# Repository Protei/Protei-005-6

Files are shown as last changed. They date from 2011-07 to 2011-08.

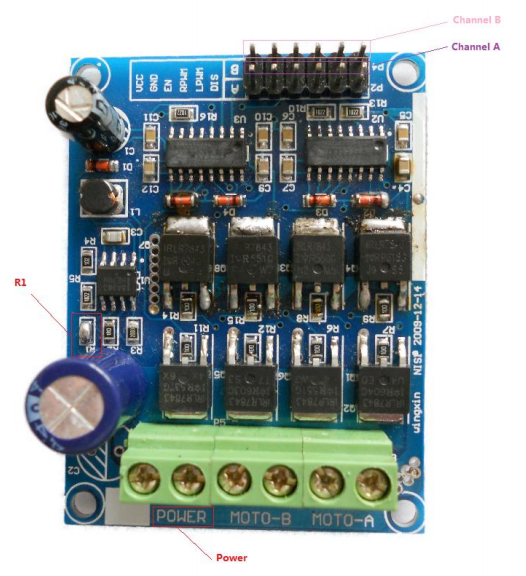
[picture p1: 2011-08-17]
Documentation/images/motordriver.png

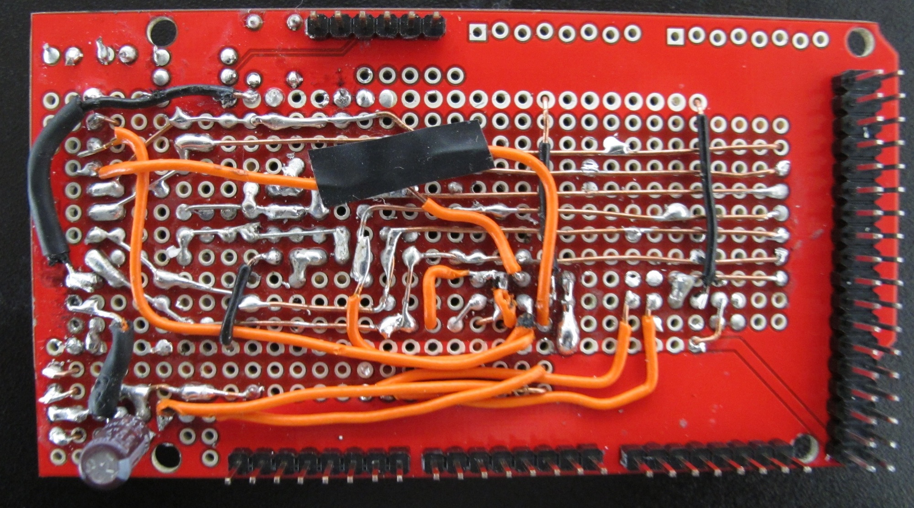
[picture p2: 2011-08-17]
Documentation/images/IMG_1639.JPG

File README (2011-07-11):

This is the git repository for the Protei project (http://protei.org).

This is  a place  for storing and  building upon code,  storing  electrical
schematics and mechanical drawings,  and for storing basically any piece of
digital information  developed for the Protei project. Storing  things here
allows us to keep a record of changes and contributions.

To gain write access to this repository, please email code@opensailing.net.

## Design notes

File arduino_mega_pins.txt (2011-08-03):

MOTOR DRIVER 1
ENA - 42
ENB - 44
RPWMA - 4
RPWMB - 5
LPWMA - 6
LPWMB - 7

MOTOR DRIVER 2
ENA - 36
RPWMA - 8
LPWMA - 9

XBEE
pin 18/19 (Serial 1)

MOTOR SENSORS
ROT1 - 2 (interrupt 0)
ROT2 - 3 (interrupt 1)
L2B - 48
L2A - 46
L1B - 40
L1A - 38
ROTWINCH - 21 (interrupt 2)
LIMITWINCH - 50git

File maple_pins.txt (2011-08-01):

MAPLE PIN		CONNECTION	REQUIRED FUNCTIONALITY	MAPLE HARDWARE DEVICE
MOTOR DRIVER 1			
4			ENA					DI/O
0			RPWMA		PWM			Timer 2
1			LPWMA		PWM			Timer 2
5			ENB					DI/O
2			RPWMB		PWM			Timer 2
3			LPWMB		PWM			Timer 2
XBEE			
7			XBDIN		Tx			USART 1
8			XBDOUT		Rx			USART 1
MOTOR DRIVER 2			
6			ENA					DI/O
11			RPWMA		PWM			Timer 3
12			LPWMA		PWM			Timer 3
MOTOR FEEDBACK			
29			ROT1		int			EXTI10
21			LIMIT1A		int			EXTI13
28			LIMIT1B		int			EXTI9
30			ROT2		int			EXTI11
22			LIMIT2A		int			EXTI14
37			LIMIT2B		int			EXTI8
31			ROTW		int			EXTI12
23			LIMITWA		int			EXTI15

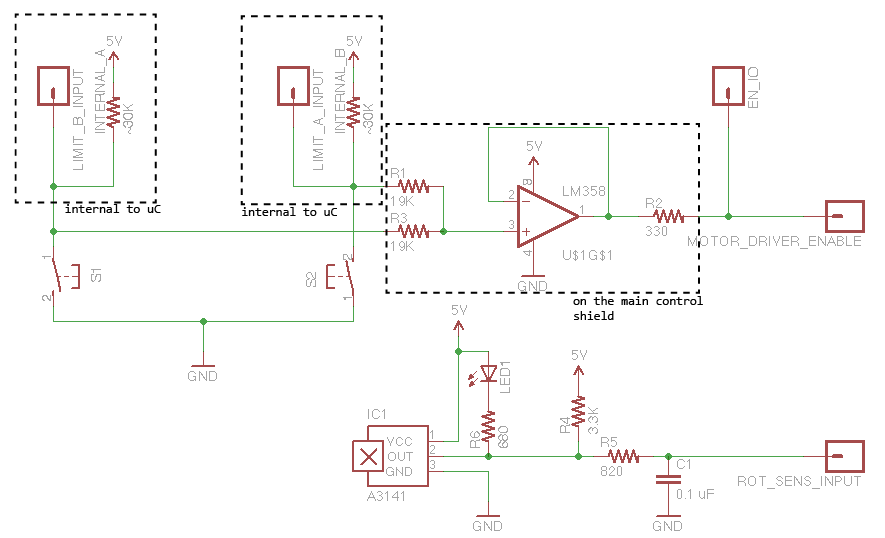
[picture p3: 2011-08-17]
Actuator/actuator.png

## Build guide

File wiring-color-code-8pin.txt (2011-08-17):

WIRING COLOR CODE : KEEL <-> CONTROL BOX

COLOR		NAME		EXPLANATION

Gray		L1A			Limit Switch A 	for motor 1
White		L1B			Limit Switch B 	for motor 1
Brown		L2A			Limit Switch A 	for motor 2
Green		L2B			Limit Switch B 	for motor 2
Yellow		ROT1		Rotation Sensor for motor 1
Blue		ROT2		Rotation Sensor for motor 2
Black		GND			Ground
Red			VCC			Power Supply +5V

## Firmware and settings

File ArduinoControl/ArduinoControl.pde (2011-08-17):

/*
	Protei — Remote Control and Motor Control
 Copyright (C) 2011  Logan Williams, Gabriella Levine,
                     Qiuyang Zhou, Francois de la Taste
 
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
 You should have received a copy of the GNU General Public License
 along with this program (see COPYING).  If not, see <http://www.gnu.org/licenses/>.
 */
 
#include "consts.h" 	        // File containing constants defininitions
#include "comm.h"	 	// File containing communication subroutines
//#include "motor.h"		// File containing motor control subroutines
#include "motor_controller.h"

// EXECUTION VARIABLES
unsigned long lastExecuted; // this variable keeps
unsigned long time; // this is a variable for the current time

// for 19 jul test

int motorNumber;
int stopwatch;

unsigned long lastBowCounted;
unsigned long lastSternCounted;

unsigned long usbElapsCounter = 0;

Motor bow;
MotorController bowController;

Motor stern;
MotorController sternController;

Motor winch;

void setup() {
  bow.init(BOW);
  bowController.init(&bow, GAIN[BOW]);
  pinMode(ROT_PINS[BOW], INPUT);
  attachInterrupt(ROT_INTS[BOW], countBow, FALLING); //was set to CHANGE... it shouldn't make a difference (but you never know)

  stern.init(STERN);
  sternController.init(&stern, GAIN[STERN]);
  pinMode(ROT_PINS[STERN], INPUT);
  attachInterrupt(ROT_INTS[STERN], countStern, FALLING);
  
  winch.init(WINCH);
  pinMode(ROT_PINS[WINCH], INPUT);

  // initialize pins
  pinMode(EN_PINS[BOW], INPUT);
  pinMode(EN_PINS[STERN], INPUT);
  pinMode(EN_PINS[WINCH], INPUT);

  pinMode(LIMIT_A_PINS[BOW], INPUT);
  pinMode(LIMIT_A_PINS[STERN], INPUT);
  pinMode(LIMIT_A_PINS[WINCH], INPUT);
  pinMode(LIMIT_B_PINS[BOW], INPUT);
  pinMode(LIMIT_B_PINS[STERN], INPUT);
  digitalWrite(LIMIT_A_PINS[BOW], HIGH);
  digitalWrite(LIMIT_A_PINS[STERN], HIGH);
  digitalWrite(LIMIT_A_PINS[WINCH], HIGH);
  digitalWrite(LIMIT_B_PINS[BOW], HIGH);
  digitalWrite(LIMIT_B_PINS[STERN], HIGH); 
  
  pinMode(LPWM_PINS[BOW], OUTPUT);
  pinMode(LPWM_PINS[STERN], OUTPUT);
  pinMode(LPWM_PINS[WINCH], OUTPUT);
  pinMode(RPWM_PINS[BOW], OUTPUT);
  pinMode(RPWM_PINS[STERN], OUTPUT);
  pinMode(RPWM_PINS[WINCH], OUTPUT);

  // start the interrupts
  interrupts(); 

  Serial1.begin(57600); // begin Xbee serial comms
  Serial.begin(115200); // begin USB serial comms
}

/*** THE MAIN LOOP ***
 * The loop body executes every 50ms, for a 20Hz control loop. This is kept in time with millis().
 */
void loop() {
  unsigned char data1 = 0x00;
  unsigned char data2 = 0x00;
  unsigned char data3 = 0x00;

  time = millis();
  
  // The main control loop executes every 50 ms (CONTROL_LOOP_PERIOD)
  if (((time - lastExecuted) > CONTROL_LOOP_PERIOD) || ((time - lastExecuted) < 0)) {
    lastExecuted = time; // update our time watch
    
    // If we have received new data from the Xbee, use it to update desired position
    if (receive(&data1, &data2, &data3)) { //fixmelater
      sendStatus(bow.getCntFlag(), stern.getCntFlag());
      //bowController.setTarget(map(data1, 0, 255, 0, MAX_MOTOR_ROTATIONS[BOW]));
      // testing two different control strategies:
      //  - closed loop position control (stern)
      //  - open loop speed control (bow)
      bow.move(map(data1, 0, 255, -255, 255));
      //stern.move(map(data2, 0, 255, -255, 255));
      //sternController.setTarget(map(data2, 0, 255, 0, MAX_MOTOR_ROTATIONS[STERN]));
      winch.move(map(data3, 0, 255, -255, 255));
    }

    //int output = bowController.runLoop();
    //int output2 = sternController.runLoop();

    if(debug && (usbElapsCounter >=  usbDebugRate) ) {
      Serial.println("BOW DEBUG DATA");
      bowController.printDebug();
      Serial.println("STERN DEBUG DATA");
      sternController.printDebug();
    }
    
    usbElapsCounter++;
  }
}

/** INTERRUPT SERVICE ROUTINES */
//    These really should be part of the Motor class
//    but the Arduino environment does not allow
//    interrupts to be defined inside objects
void countBow() {
  if (millis() - lastBowCounted > 40 || millis() - lastBowCounted < 0) { // this essentially "debounces" our rotation sensor
    if (digitalRead(ROT_PINS[BOW]) == LOW) { // double check
      lastBowCounted = millis(); // reset the timer
      bow.count(); // modify the counter accordingly
    }
  }
}

/* this is the same as above */
void countStern() {
  if (millis() - lastSternCounted > 40 || millis() - lastSternCounted < 0) {
    if (digitalRead(ROT_PINS[STERN]) == LOW) {
      lastSternCounted = millis();
      stern.count();
    }
  }
}

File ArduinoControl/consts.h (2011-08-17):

/*
	Protei — Remote Control and Motor Control
 Copyright (C) 2011  Logan Williams, Gabriella Levine,
                     Qiuyang Zhou, Francois de la Taste
 
 	This file is part of Protei.
 	
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
 You should have received a copy of the GNU General Public License
 along with this program (see COPYING).  If not, see <http://www.gnu.org/licenses/>.
 */

/** CONSTANT DEFINITIONS */

// Motors are indexed as follow :
//  0 - bow articulation motor
//  1 - stern articulation motor
//  2 - sail whinch motor
#define   BOW   0
#define   STERN 1
#define   WINCH 2

// this needs to be measured and set manually
const int MAX_MOTOR_ROTATIONS[] = {
  101, 103, 100};

const int GAIN[] = {
  70, 70, 35}; // the proportional gain

// PIN DEFINITIONS
// motor drivers
const int EN_PINS[] 	= {
  42, 44, 36};
const int RPWM_PINS[] 	= {
  5, 4, 8};
const int LPWM_PINS[] 	= {
  6, 7, 9};
// xbee

const int XBEE_TX_PIN = 18;
const int XBEE_RX_PIN = 19;

// motor feedback interrupt pins
const int ROT_PINS[] 		= {
  2, 3, 21};
const int ROT_INTS[] = {
  0, 1, 2};
const int LIMIT_A_PINS[] 	= {
  38, 46, 50};
const int LIMIT_B_PINS[] 	= {
  40, 48}; // the winch does not have a Limit B switch

// the control loop period in ms. 50ms == 20hz
const int CONTROL_LOOP_PERIOD = 50;

// the period of printing debug info over usb
// = usbDebugRate * CONTROL_LOOP_PERIOD = 250ms
const int usbDebugRate = 20;

// the current debug level (higher numbers mean
// that more information is printed)
const int debug = 6;

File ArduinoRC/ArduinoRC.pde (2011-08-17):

/*
	Protei — Remote Control and Motor Control
 Copyright (C) 2011  Logan Williams, Gabriella Levine,
                     Qiuyang Zhou, Francois de la Taste
 
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
 You should have received a copy of the GNU General Public License
 along with this program (see COPYING).  If not, see <http://www.gnu.org/licenses/>.
 */
 
// system constants
const int JOYSTICK_LEFT_IN = 0;
const int JOYSTICK_RIGHT_IN = 1;

// sketch variables
int sensorValueJSL;
int outputValueJSL;
int sensorValueJSR;
int outputValueJSR;
int outputValueButtons;

int toggle = HIGH;

int inc = 4;

void setup() {
  pinMode(2, INPUT);
  digitalWrite(2, HIGH);
  pinMode(3, INPUT);
  digitalWrite(3, HIGH);
  
  pinMode(4, OUTPUT);
  pinMode(5, OUTPUT);
  pinMode(6, OUTPUT);
  pinMode(7, OUTPUT);
  pinMode(8, OUTPUT);
  pinMode(9, OUTPUT);
  pinMode(10, OUTPUT);
  pinMode(11, OUTPUT);
  
  digitalWrite(10, HIGH); // power
  
  Serial.begin(9600); // initialize serial
}

void loop() {
  unsigned char senseData;
  int limitABOW = 0;
  int limitBBOW = 0;
  int rotBOW = 0;
  int limitASTERN = 0;
  int limitBSTERN = 0;
  int rotSTERN = 0;
  
    if (receive(&senseData)) {
    limitBSTERN = senseData & B00010000;
    rotSTERN = senseData & B00100000;
    limitABOW = senseData & B00001000;
    rotBOW = senseData & B00000100;
    limitBBOW = senseData & B00000010;
    limitASTERN = senseData & B00000001;
    
    digitalWrite(5, limitASTERN);
    digitalWrite(6, limitBSTERN);
    digitalWrite(7, rotSTERN);
    digitalWrite(8, limitBBOW);
    digitalWrite(9, rotBOW);
    digitalWrite(11, limitABOW);
    digitalWrite(4, toggle);
    
    if (toggle == HIGH) {
      toggle = LOW;
    } else {
      toggle = HIGH;
    }
  }
  
  sensorValueJSL = analogRead(JOYSTICK_LEFT_IN); // read the left joystick
  outputValueJSL = mapWell(sensorValueJSL, 70, 1023, 0, 255); // map it to 8 bit values
  
  sensorValueJSR = analogRead(JOYSTICK_RIGHT_IN); // repeat for right joystick
  outputValueJSR = mapWell(sensorValueJSR, 0, 1012, 0, 255);
  
  if (digitalRead(2) == LOW && digitalRead(3) == HIGH) {
    outputValueButtons = 22;
  } else if (digitalRead(3) == LOW && digitalRead(2) == HIGH) {
    outputValueButtons = 232;
  } else {
    outputValueButtons = 127;
  }
  
  sendBytes(outputValueJSL, outputValueJSR, outputValueButtons); // transmit the values
  

  
  delay(100);
  
    
}

boolean receive(unsigned char *data1) {
  unsigned char byteRead;
  unsigned char halfByte1A;
  unsigned char halfByte1B;
  unsigned char buffer[128];
  unsigned char toSend1;
  unsigned char toSend2;
  int i = 0;
  int start;
  int avail = Serial.available();

  if (avail > 8) {
    for (i = 0; (i < avail) && (i < 128); i++) {
      buffer[i] = Serial.read();
    }
  
    for (int j = 0; j < i; j++) {
      if (buffer[j] == 'S') {
        start = j;
      }
    }
    
    if (start+3 <= i) {
      halfByte1A = buffer[start+1];
      halfByte1B = buffer[start+2];
      byteRead = buffer[start+3];
      
      
          
      if (byteRead == 'E') { // end byte recieved successfully
        halfByte1A = hamming74Decode(halfByte1A);
        halfByte1B = hamming74Decode(halfByte1B);
      
        if (halfByte1A == 0xFF || halfByte1B == 0xFF) {
          // multiple bit errors, recovery impossible
      
          return false;
        } 
        else {
          *data1 = (halfByte1A & B00001111) + ((halfByte1B << 4) & B11110000);
          return true;     
        }
      }
    } else {
      return false;
    }
  } else {
    return false;
  }
}
  
// TRANSMITS JOYSTICK VALUES
//  uses a Hamming(7,4) code with overall parity bit
//  splits two input bytes into 4 bit halfbytes
//  transmits:
//    - 'S' // start bit
//    - [Hamming encoded Halfbyte1A]
//    - ...
//    - 'E' // stop bit
void sendBytes(char byte1, char byte2, char byte3) {
  char halfByte1A = byte1 & B00001111;
  char halfByte1B = (byte1 >> 4) & B00001111;
  char halfByte2A = byte2 & B00001111;
  char halfByte2B = (byte2 >> 4) & B00001111;
  char halfByte3A = byte3 & B00001111;
  char halfByte3B = (byte3 >> 4) & B00001111;
  
  Serial.write('S');
  Serial.write(hamming74Encode(halfByte1A));
  Serial.write(hamming74Encode(halfByte1B));
  Serial.write(hamming74Encode(halfByte2A));
  Serial.write(hamming74Encode(halfByte2B));
  Serial.write(hamming74Encode(halfByte3A));
  Serial.write(hamming74Encode(halfByte3B));
  Serial.write('E');
  
  return;
}

// converts a 4 bit halfbyte to its 8 bit hamming encoded version
// I know, it's a lookup table. whatever, I'll fix it if I have to
char hamming74Encode(char halfByte) {
  halfByte = halfByte & B00001111;
  
  switch(halfByte) {
    case B0000:
      return B00000000;
    case B0001:
      return B00010111;
    case B0010:
      return B00101011;
    case B0011:
      return B00111100;
    case B0100:
      return B01001101;
    case B0101:
      return B01011010;
    case B0110:
      return B01100110;
    case B0111:
      return B01110001;
    case B1000:
      return B10001110;
    case B1001:
      return B10011001;
    case B1010:
      return B10100101;
    case B1011:
      return B10110010;
    case B1100:
      return B11000011;
    case B1101:
      return B11010100;
    case B1110:
      return B11101000;
    case B1111:
      return B11111111;
    return B0000;
  }
}

int mapWell(int val, int lval, int hval, int lout, int hout) {
  if (val < lval) {
    return lout;
  } else if (val > hval) {
    return hout;
  } else {
    return map(val, lval, hval, lout, hout);
  }
}
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

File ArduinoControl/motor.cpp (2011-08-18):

/*
	Protei — Remote Control and Motor Control
 Copyright (C) 2011  Logan Williams, Gabriella Levine,
                     Qiuyang Zhou, Francois de la Taste
 
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
 You should have received a copy of the GNU General Public License
 along with this program (see COPYING).  If not, see <http://www.gnu.org/licenses/>.
 */

#include "motor.h"
#include "consts.h"
#include "WProgram.h"

/* empty constructor */
Motor::Motor() {
}

/* helper constructor */
Motor::Motor(int motor) {
  init(motor);
}

/* init() takes one argument:
     int motor -- the motorNumber that the object
       is commanding */
void Motor::init(int motor) {
  motorNumber = motor;
  pinMode(EN_PINS[motorNumber], INPUT);
  rotations = MAX_MOTOR_ROTATIONS[motorNumber]/2;
  pinMode(ROT_PINS[motorNumber], INPUT);
}

/* a helper function for when we are not
   calibrating the motor */
int Motor::move(int speed) {
  move(speed, false);
}

/* move(int speed, int calibrating) is a function
   for driving the motor at a specified value. it
   takes two arguments:
     int speed -- the speed, between -65535 and 65535
       that we wish to drive the motor
     int calibrating -- whether or not we are calibrating
       the motor. 0 (false) if not calibrating, 1 (true)
       otherwise */
int Motor::move(int moveSpeed, int calibrating) {
  // are we changing direction?
  if ((currentSpeed > 0 && moveSpeed < 0) || (currentSpeed < 0 && moveSpeed > 0)) {
    if (digitalRead(ROT_PINS[motorNumber]) == LOW) {
      // don't change direction if the rotation sensor is on
      moveSpeed = currentSpeed;
    } else { 
      // otherwise, make sure we stop for at least 250 milliseconds before reversing
      // (to ensure that rotations are counted correctly)
      if (moveSpeed > 4) {
        moveSpeed = 4;
      } else if (moveSpeed > 0) {
        moveSpeed -= 1;
      } else if (moveSpeed < -4) {
        moveSpeed = -4;
      } else if (moveSpeed < 0) {
        moveSpeed += 1;
      }
    }
  }
  
  // if we are not changing direction, we accept the
  // speed provided
  currentSpeed = moveSpeed;
 
   // read the status of the limit switches
  int limitA = digitalRead(LIMIT_A_PINS[motorNumber]);
  int limitB = digitalRead(LIMIT_B_PINS[motorNumber]);
  
  if ((limitA == LOW) || (limitB == LOW)) {
    if ((limitA == LOW) && ((*this).getDirection() == -1)) {
      // if we are running into limit A, brake, and reset the rotation
      // sensor to the lower limit (unless in calibration mode)
      brake();
      if (0 == calibrating) {
        resetLimitLow();
      }
      
      // return -1000 to indicate that we ran into the lower limit sensor (A)
      return -1000; 
    } else if ((limitB == LOW) && ((*this).getDirection() == 1)) {
      // if we are running into Limit B, brake, and reset the rotaiton
      // sensor to the upper limit (unless in calibration mode)
      brake();
      if (0 == calibrating) {
        resetLimitHigh();
      }
      
      // return 1000 to indicate that we ran into the lower limit sensor (B)
      return 1000;
    } else {
      // other wise, we are moving away from the limit sensor that has been pressed.
      
      // this is okay, so re-enable the motor driver
      pinMode(EN_PINS[motorNumber], OUTPUT);
      digitalWrite(EN_PINS[motorNumber], HIGH);
    }
  } else {
    // if no limit switches are pressed, the motor driver enable mode should be passive
    // (controlled by limit switches)
    pinMode(EN_PINS[motorNumber], INPUT);
  }
  
  // send PWM data to the motor controller, unless the speed is very slow, in which case
  // we tell the motor controller to brake
  if (moveSpeed > 30) {
    digitalWrite(RPWM_PINS[motorNumber], HIGH);
    analogWrite(LPWM_PINS[motorNumber], 255 - moveSpeed);
  } else if (moveSpeed < -30) {
    digitalWrite(LPWM_PINS[motorNumber], HIGH);
    analogWrite(RPWM_PINS[motorNumber], 255 + moveSpeed);
  } else {
    brake();
  }
  
  return moveSpeed;
}

/* brake() commands the motor driver to brake
   the motor. */
void Motor::brake() {
  digitalWrite(RPWM_PINS[motorNumber], HIGH);
  digitalWrite(LPWM_PINS[motorNumber], HIGH);
  currentSpeed = 0;
}

/* return the current speed */
int Motor::getSpeed() {
  return currentSpeed;
}

/* by checking the current output speed, this returns
   1 if moving in a positive direction (towards limit B)
   and 0 otherwise */
int Motor::getDirection() {
  if (currentSpeed > 0) {
    return 1;
  } else if (currentSpeed < 0) {
    return -1;
  } else {
    return 0;
  }
}

/* return the current number of rotations */
int Motor::getRotations() {
  return rotations;
}

/* reset the current number of rotations to minimum */
int Motor::resetLimitLow() {
  rotations = 0;
  return 0;
}

/* reset the current number of rotations to maximum */
int Motor::resetLimitHigh() {
  rotations = MAX_MOTOR_ROTATIONS[motorNumber];
  return rotations;
}

/* count() increments or decrements the rotation counter
   depending on the direction the motor is spinning */
void Motor::count() {
  if (getDirection() == 1) {
    rotations++;
  } 
  else if (getDirection() == -1) {
    rotations--;
  }
  
  cntFlag = 1; // set the cntFlag for the status information
}

/* Because the rotation sensor only goes low for a very
   short period of time, this function returns 1 (true)
   if the function has been called for the first time since
   the sensor has been triggered. This is used for sending
   status information back to the joystick controller. */
int Motor::getCntFlag() {
  if (cntFlag == 1) {
    cntFlag = 0;
    return true;
  }
  
  return false;
}

/* calibrate() tests the linear actuators by moving
   the actuator from one end of its range to the other
   at both low speeds and high speeds, measuring the
   total rotations that the counter counts. */
int Motor::calibrate() {
  int totalRotations = 0;
  
  // move the carriage to the low position
  while (move(-170) != -1000);
  
  // then, move it back towards the high position (in calibration mode)
  while (move(170, 1) != 1000);
  
  Serial.println(rotations);
  totalRotations += rotations;
  rotations = 0;
  
  // count again, going back to the low position
  while (move(-170, 1) != -1000);
  
  Serial.println(rotations);
  totalRotations -= rotations;
  rotations = 0;
  
  // repeat the above again, this time at full speed
  while (move(255, 1) != 1000);
  
  Serial.println(rotations);
  totalRotations += rotations;
  rotations = 0;
  
  while (move(-255, 1) != -1000);
  
  Serial.println(rotations);
  totalRotations -= rotations;
 
  // return the average rotation count
  return (totalRotations/4);
}

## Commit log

2011-07-01 Added code to read the ADC on the ArduPilot IMU board with the Maple
2011-07-08 LSM303DLH pololu carrier board
2011-07-11 adding prototype controller code (never tested on real hardware BEWARE)
2011-07-19 Split routines into different files and added prototypes
    - Separed subroutines into different header files : PID, motors, constan
    ts, communication
    - Added function prototypes
2011-07-19 corrected an error in motor control
    motor command on negative values should be 65535 + val, instead of 0 - v
    al
2011-07-21 Added classes for Motors and MotorControllers, removed the Rotational Sensor class (unnecessary), and cleaned up formatting
2011-07-21 added motor classes
2011-07-22 update current testing version
2011-07-27 Motor control code working reliabily
2011-07-29 added more documentation -- fixed names in header
    [consts.h, motor.cpp, motor_controller.cpp]
2011-08-01 Added control board schematics
2011-08-01 Updated schematic
    [MegaShield.brd, MegaShield.sch]
2011-08-03 Ported maple control code to the Arduino Mega
2011-08-12 added wiring color code for 8pin connector between keel and control box
2011-08-17 Updated comments, added Acuator schematics, added some initial documentation (and images) done in LyX
    [actuator.sch]
2011-08-18 keep it current :)
